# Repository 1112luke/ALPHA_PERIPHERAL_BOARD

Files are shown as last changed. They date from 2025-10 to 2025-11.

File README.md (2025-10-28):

<h1 align="center">🥵🚀NDXP Alpha Peripheral Board🚀🌡️</h1>

<p align="center">
  Screenshot 2025-10-28 at 10 34 32 AM

</p>

<h4 align="center">This is the repository for the HARDWARE DESIGN ONLY. Software for the board can be found <a href="https://github.com/1112luke/NDXPCOMPUTER">here</a></h4>

## Introduction

This board was developed for NDXP's Alpha engine. Its purpose is to serve as a peripheral board to the [F.E.R.B.](https://github.com/1112luke/NDXPCOMPUTER) flight computer, and will facilitate data collection for the secifics of the Alpha mission. The board is responsible for collecting pressure and temperature data on the engine, as well as accelerometer data and load cell data during ground testing.

## Specifications

The board has capability in data collection, communication, actuation, and failsafe:

### Data Collection
- 12x 0-5v ADC (used for pressure sensing)
- 4x Thermocouple Channels
- 1x I2C accelerometer interface
- 1x Load Cell Interface

### Communication
- 1x RS-485 Channel (for communication with  [F.E.R.B.](https://github.com/1112luke/NDXPCOMPUTER))
- 1x Serial USB Port

### Actuation
- 4x Solenoid Valve Channels
- 1x Pyro Channel

### Failsafe
- 2x Keyed Switches (Pyro, Solenoids)
- 1x Burnwire Ignition Detection
- 1x E-STOP

## Contributors
- Luke Scholler
- Sebastian Brock

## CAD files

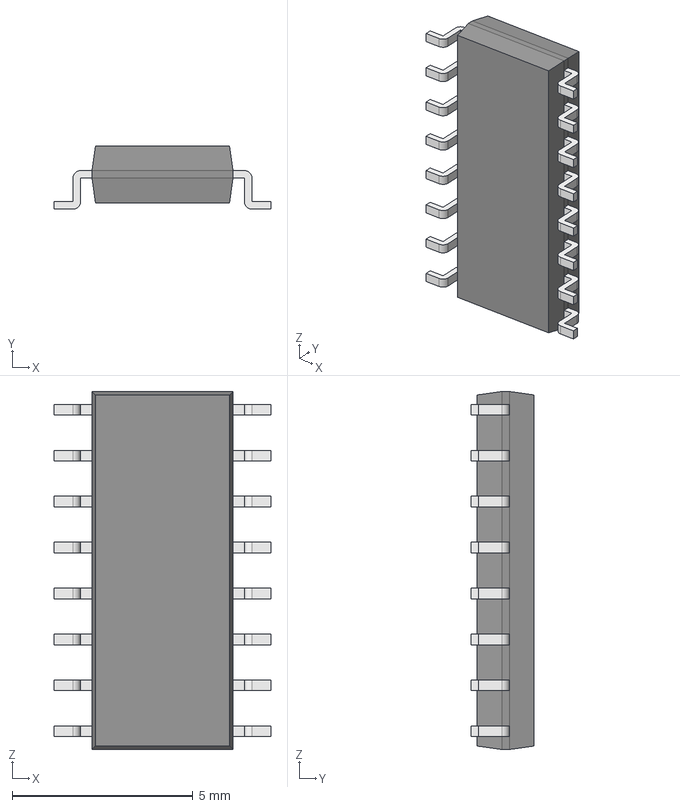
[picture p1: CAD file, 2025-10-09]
Custom_Parts/ADS1231ID/ADS1231ID.step
6.00 x 1.75 x 9.90 mm
Body001 (Mirror #1) x 8
XY-plane x 12
X-axis x 12

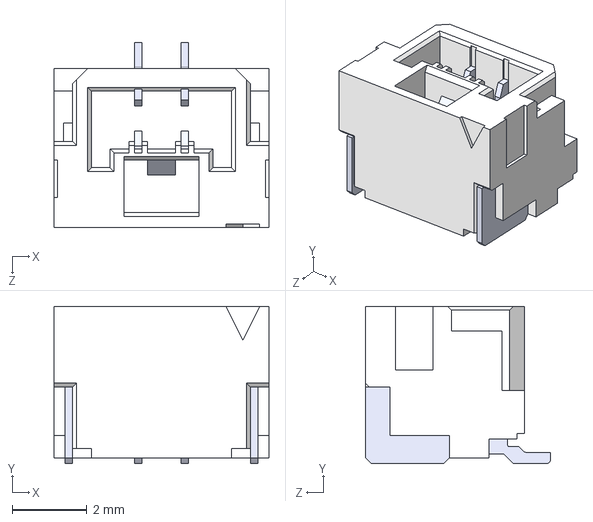
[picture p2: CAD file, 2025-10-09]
Custom_Parts/BM02B-GHS/BM02B-GHS-TBT_LF__SN_.step
5.75 x 4.20 x 4.95 mm

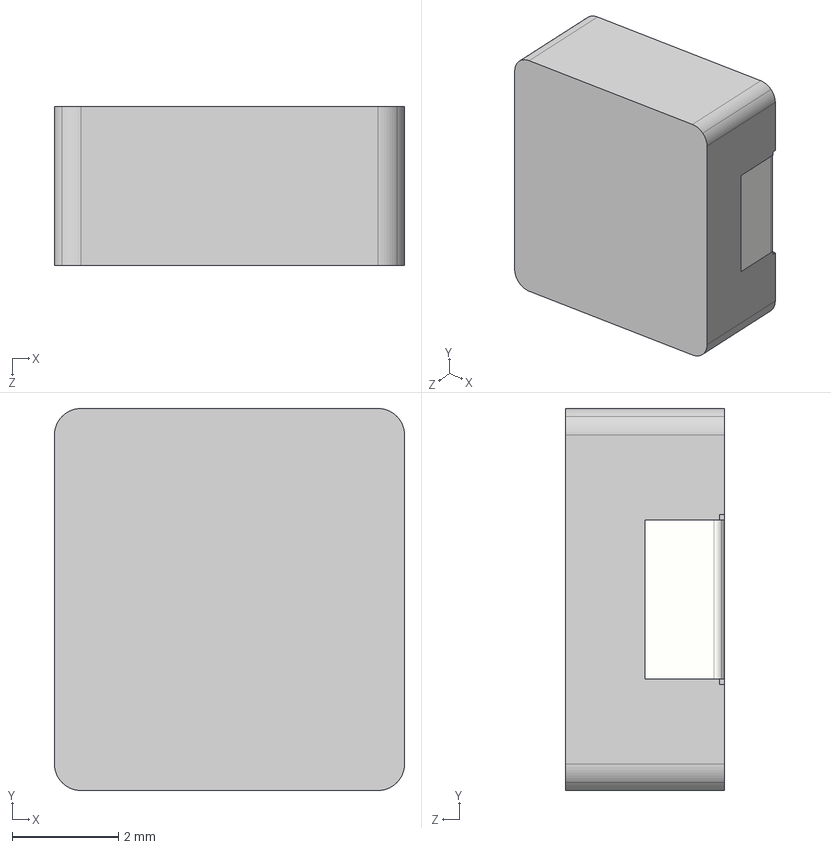
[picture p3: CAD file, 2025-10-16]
Custom_Parts/CYA0630-1.5UH/User Library-L_ShouHan_CYA0630.STEP
6.60 x 7.20 x 3.00 mm

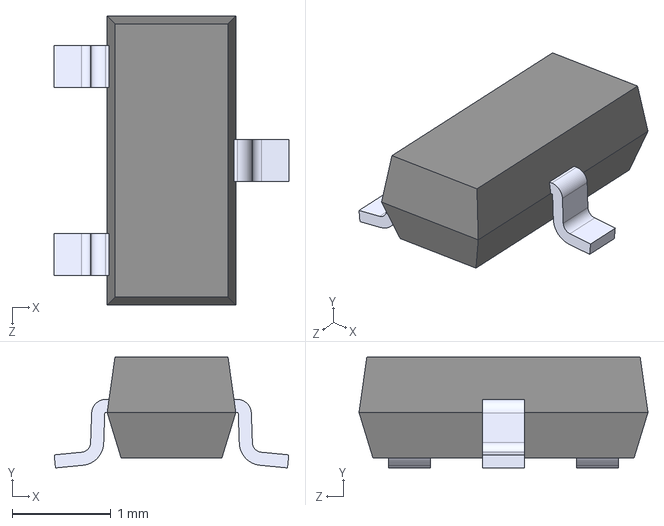
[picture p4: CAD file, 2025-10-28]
Custom_Parts/SI2302/SI2302.step
2.37 x 1.12 x 2.92 mm

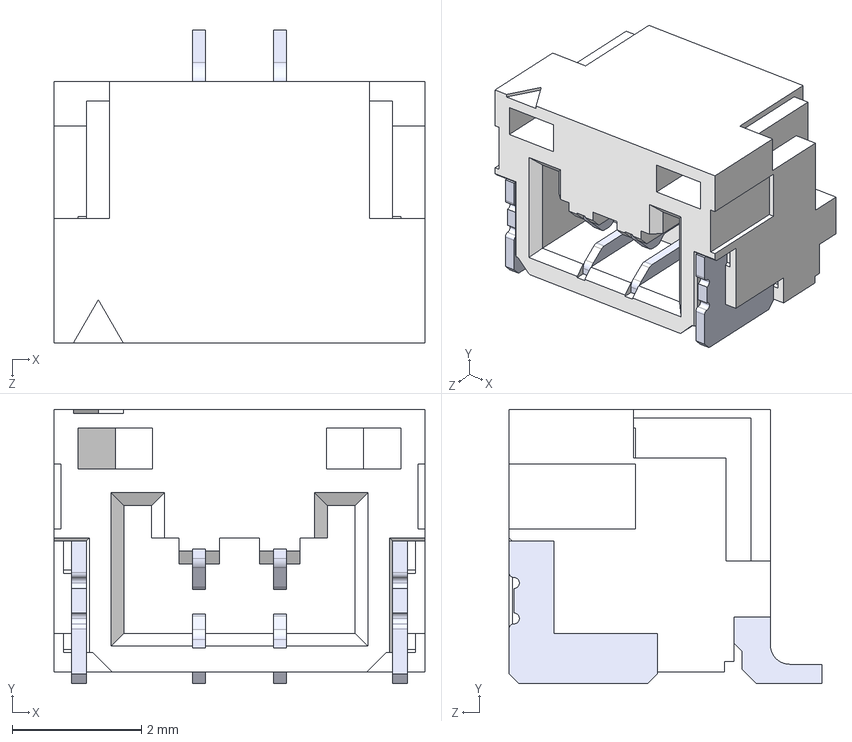
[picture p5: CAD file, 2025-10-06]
Custom_Parts/SM02B-GHS/SM02B-GHS.step
5.75 x 4.25 x 4.85 mm
SMxB-GHS-TB_02
pin x 2

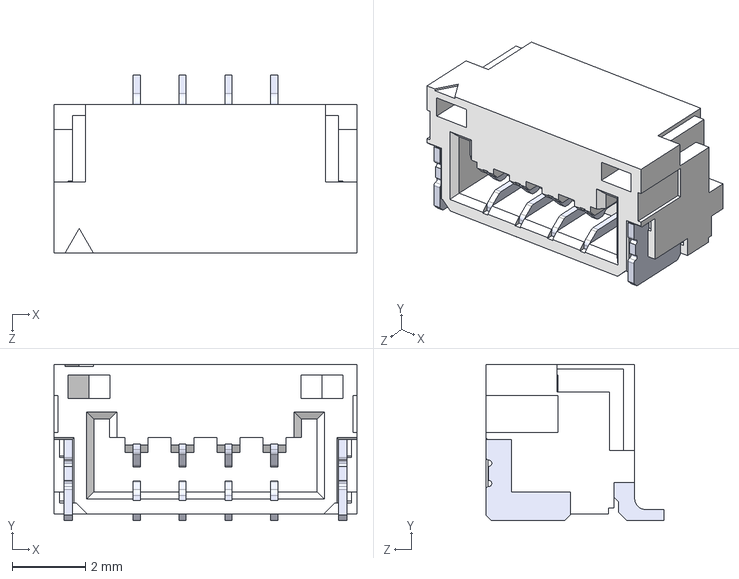
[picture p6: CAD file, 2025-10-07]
Custom_Parts/SM04B-GHS/SM04B-GHS-TB_LF__SN_-.step
8.25 x 4.25 x 4.85 mm
SMxB-GHS-TB_04
pin x 4

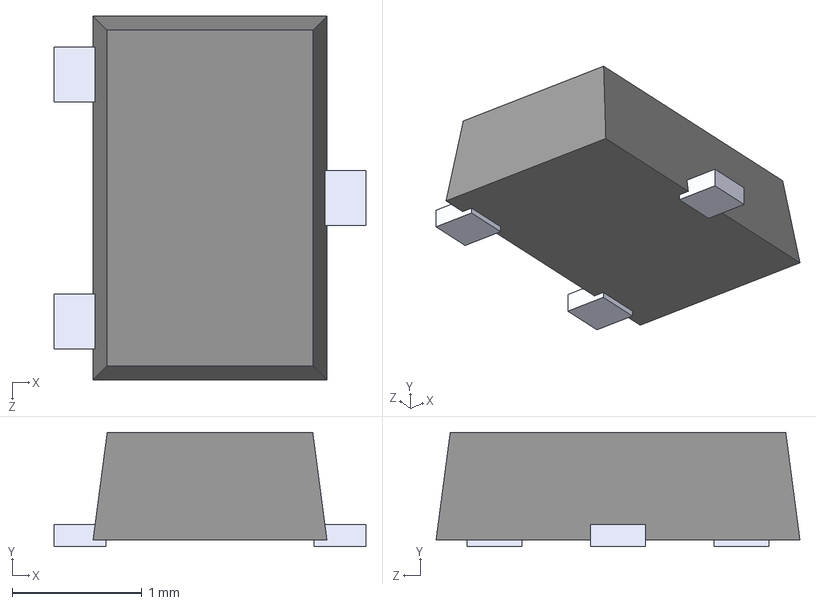
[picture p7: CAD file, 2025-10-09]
Custom_Parts/SSM3J328R/SSM3J328R_LF.step
2.40 x 0.88 x 2.80 mm

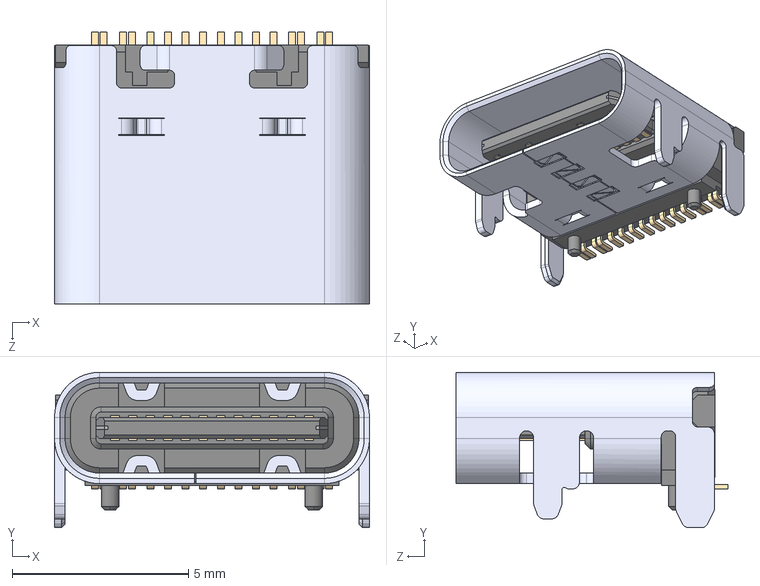
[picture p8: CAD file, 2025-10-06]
Custom_Parts/USB-C/step file.step
8.94 x 4.41 x 7.71 mm

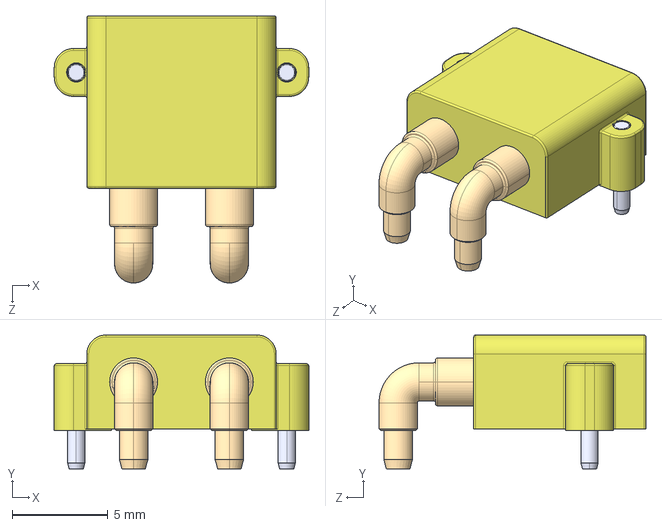
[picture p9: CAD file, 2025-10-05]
Custom_Parts/XT-30/step file.step
13.3 x 7.00 x 14.0 mm

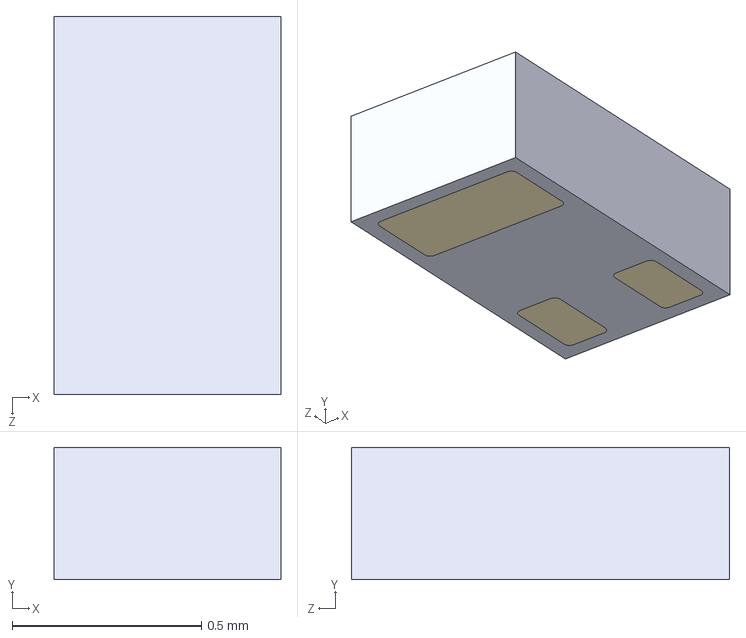
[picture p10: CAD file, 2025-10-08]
Custom_Parts/CSD13381F4/CSD13381F4.step
0.6 x 0.35 x 1.00 mm

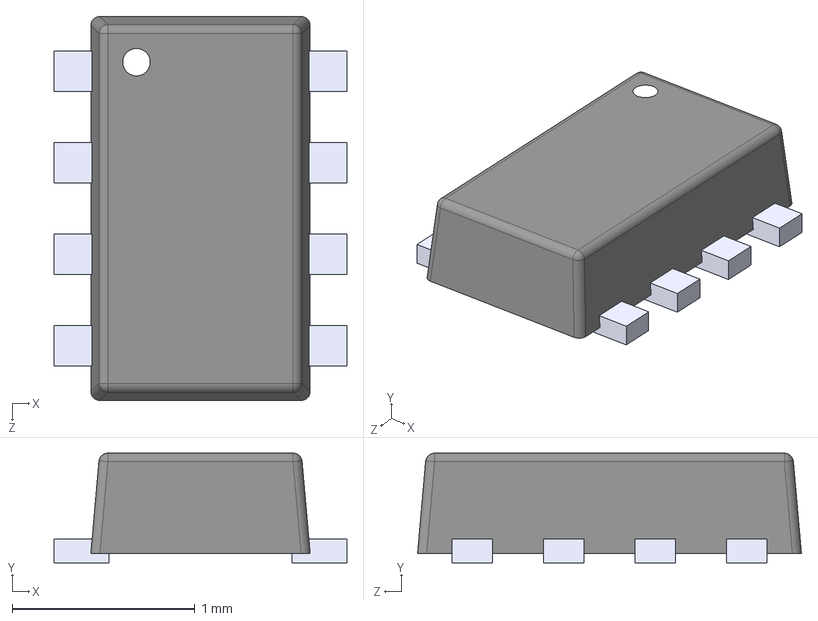
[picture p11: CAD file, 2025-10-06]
Custom_Parts/LM66200DRLR/LM66200DRLR.step
1.60 x 0.6 x 2.10 mm

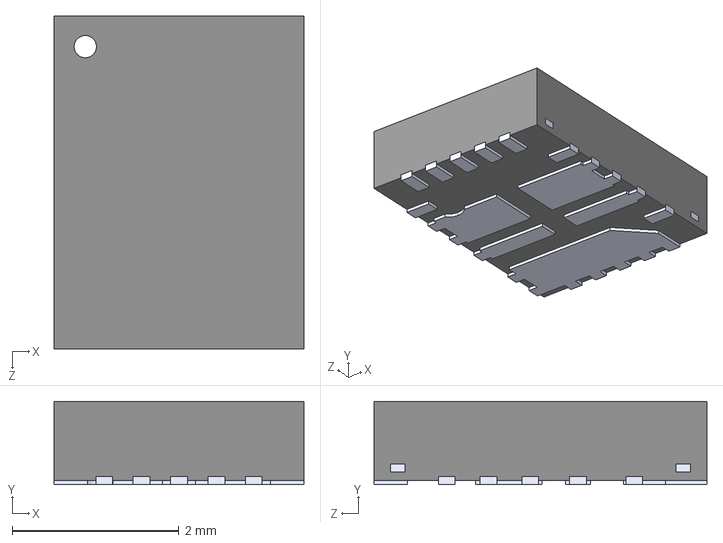
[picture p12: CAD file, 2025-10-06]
Custom_Parts/TPS513885VABR/TPS513885VABR.step
3.00 x 1.00 x 4.00 mm

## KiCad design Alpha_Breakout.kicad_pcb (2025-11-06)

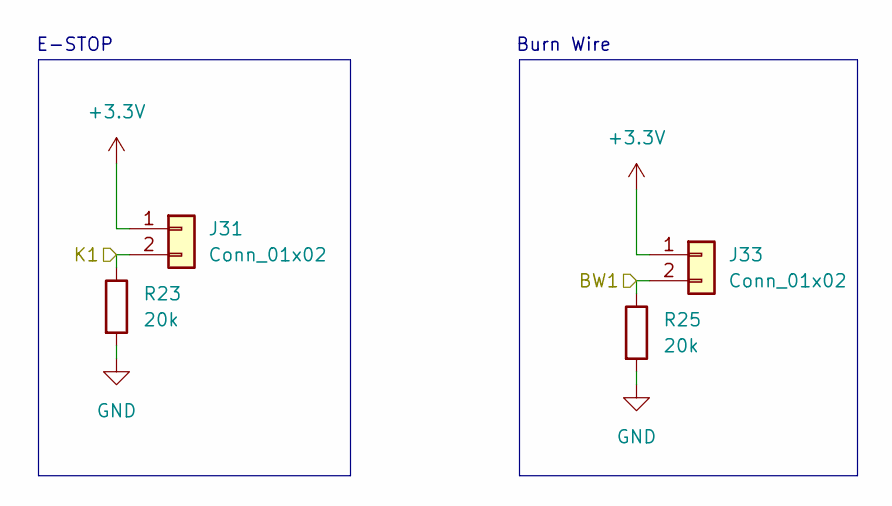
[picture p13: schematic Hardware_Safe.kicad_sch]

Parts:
J31, J33: Conn_01x02; JST_BM02B-GHS-TBT_LF__SN_; JLC# C161690
R23, R25: 20k; R_0402_1005Metric

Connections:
+3.3V: J31.1, J33.1; also elsewhere on the board
/Hardware_Safe/BW1: J33.2, R25.1; also elsewhere on the board
/Hardware_Safe/K1: J31.2, R23.1; also elsewhere on the board
GND: R23.2, R25.2; also elsewhere on the board

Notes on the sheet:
E-STOP
Burn Wire

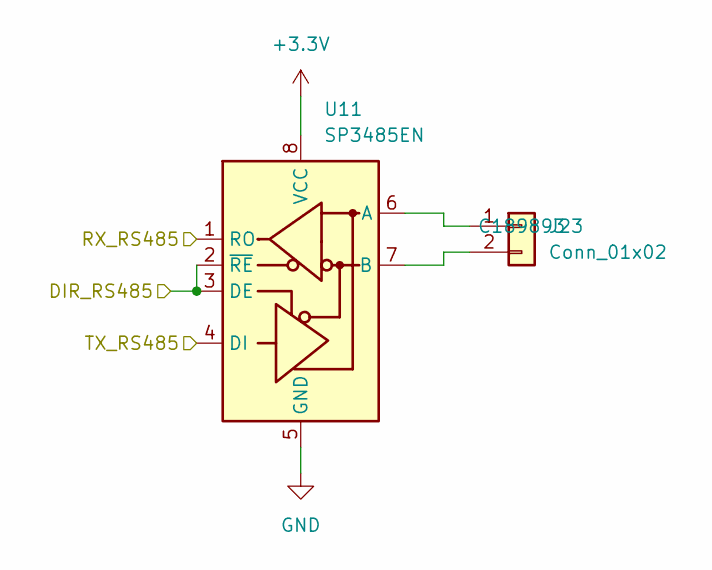
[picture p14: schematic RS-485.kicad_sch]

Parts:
J23: Conn_01x02; CONN_SM02B-GHS_JST; JLC# C189893
U11: SP3485EN; SOIC-8_3.9x4.9mm_P1.27mm; JLC# C8963

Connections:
+3.3V: U11.8 (VCC); also elsewhere on the board
/RS-485/DIR_RS485: U11.2 (~RE), U11.3 (DE); also elsewhere on the board
/RS-485/RX_RS485: U11.1 (RO); also elsewhere on the board
/RS-485/TX_RS485: U11.4 (DI); also elsewhere on the board
GND: U11.5 (GND); also elsewhere on the board
unnamed: J23.1, U11.6 (A)
unnamed: J23.2, U11.7 (B)

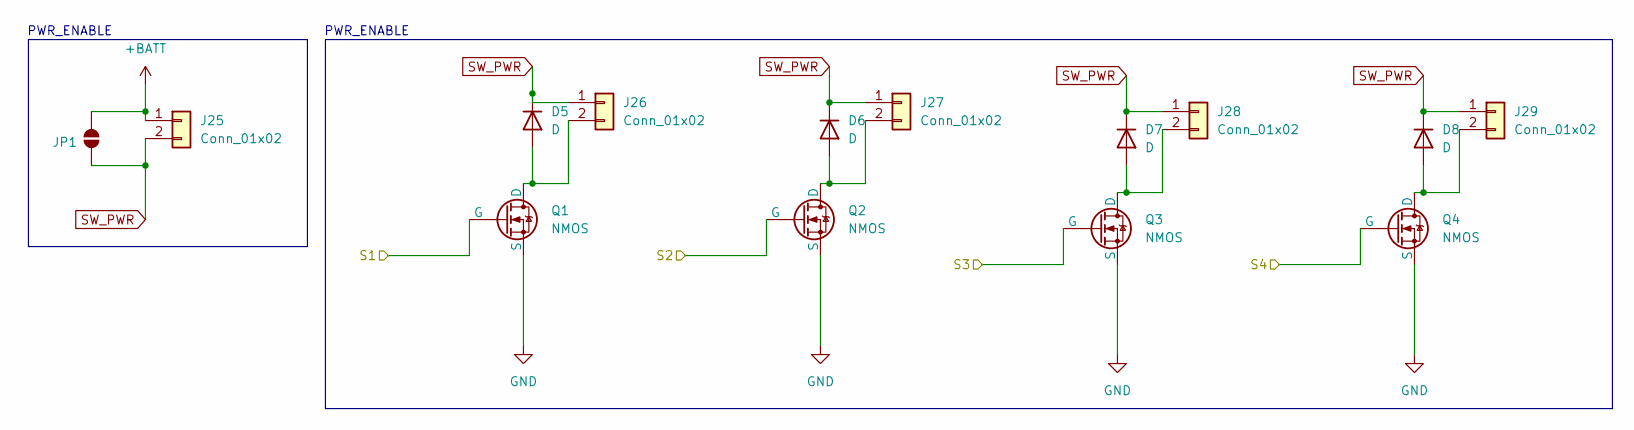
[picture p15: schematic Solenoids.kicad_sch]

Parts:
D5, D6, D7, D8: D; D_SMA; JLC# C8678
J25: Conn_01x02; JST_BM02B-GHS-TBT_LF__SN_; JLC# C161690
J26, J27, J28, J29: Conn_01x02; TerminalBlock_Phoenix_MPT-0,5-2-2.54_1x02_P2.54mm_Horizontal; JLC# C918120
JP1: SolderJumper_2_Open; SolderJumper-2_P1.3mm_Open_TrianglePad1.0x1.5mm
Q1, Q2, Q3, Q4: NMOS; SOT23; JLC# C2891732

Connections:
+BATT: J25.1, JP1.1 (A); also elsewhere on the board
/Solenoids/S1: Q1.2 (G); also elsewhere on the board
/Solenoids/S2: Q2.2 (G); also elsewhere on the board
/Solenoids/S3: Q3.2 (G); also elsewhere on the board
/Solenoids/S4: Q4.2 (G); also elsewhere on the board
GND: Q1.3 (S), Q2.3 (S), Q3.3 (S), Q4.3 (S); also elsewhere on the board
unnamed: D5.2 (A), J26.2, Q1.1 (D)
unnamed: D6.2 (A), J27.2, Q2.1 (D)
unnamed: D7.2 (A), J28.2, Q3.1 (D)
unnamed: D8.2 (A), J29.2, Q4.1 (D)
SW_PWR: D5.1 (K), D6.1 (K), D7.1 (K), D8.1 (K), J25.2, J26.1, J27.1, J28.1, J29.1, JP1.2 (B)

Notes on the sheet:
PWR_ENABLE

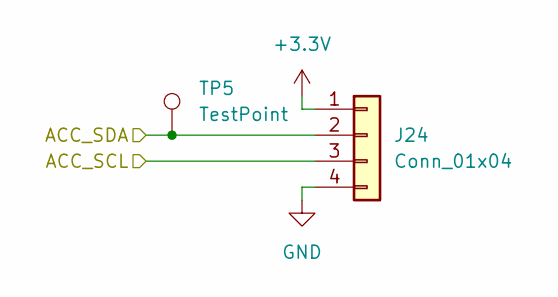
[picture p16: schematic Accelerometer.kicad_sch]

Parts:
J24: Conn_01x04; JST_GH_SM04B-GHS-TB_1x04-1MP_P1.25mm_Horizontal; JLC# C189895
TP5: TestPoint; TestPoint_Pad_D1.0mm

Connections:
+3.3V: J24.1; also elsewhere on the board
/Accelerometer/ACC_SCL: J24.3; also elsewhere on the board
/Accelerometer/ACC_SDA: J24.2, TP5.1; also elsewhere on the board
GND: J24.4; also elsewhere on the board

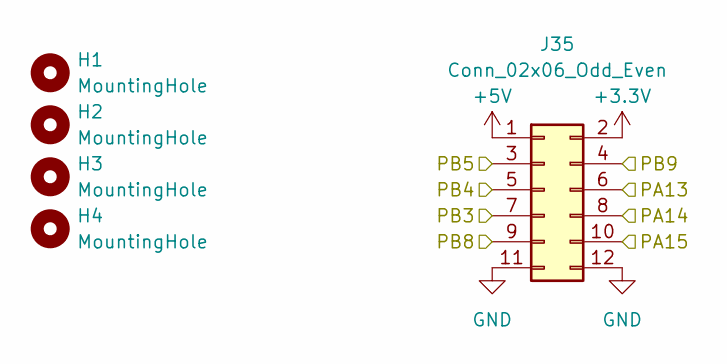
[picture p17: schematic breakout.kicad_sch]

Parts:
H1, H2, H3, H4: MountingHole; MountingHole_2.2mm_M2_DIN965_Pad
J35: Conn_02x06_Odd_Even; PinHeader_2x06_P2.54mm_Vertical

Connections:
+3.3V: J35.2; also elsewhere on the board
+5V: J35.1; also elsewhere on the board
/Breakout/PA13: J35.6; also elsewhere on the board
/Breakout/PA14: J35.8; also elsewhere on the board
/Breakout/PA15: J35.10; also elsewhere on the board
/Breakout/PB3: J35.7; also elsewhere on the board
/Breakout/PB4: J35.5; also elsewhere on the board
/Breakout/PB5: J35.3; also elsewhere on the board
/Breakout/PB8: J35.9; also elsewhere on the board
/Breakout/PB9: J35.4; also elsewhere on the board
GND: J35.11, J35.12; also elsewhere on the board

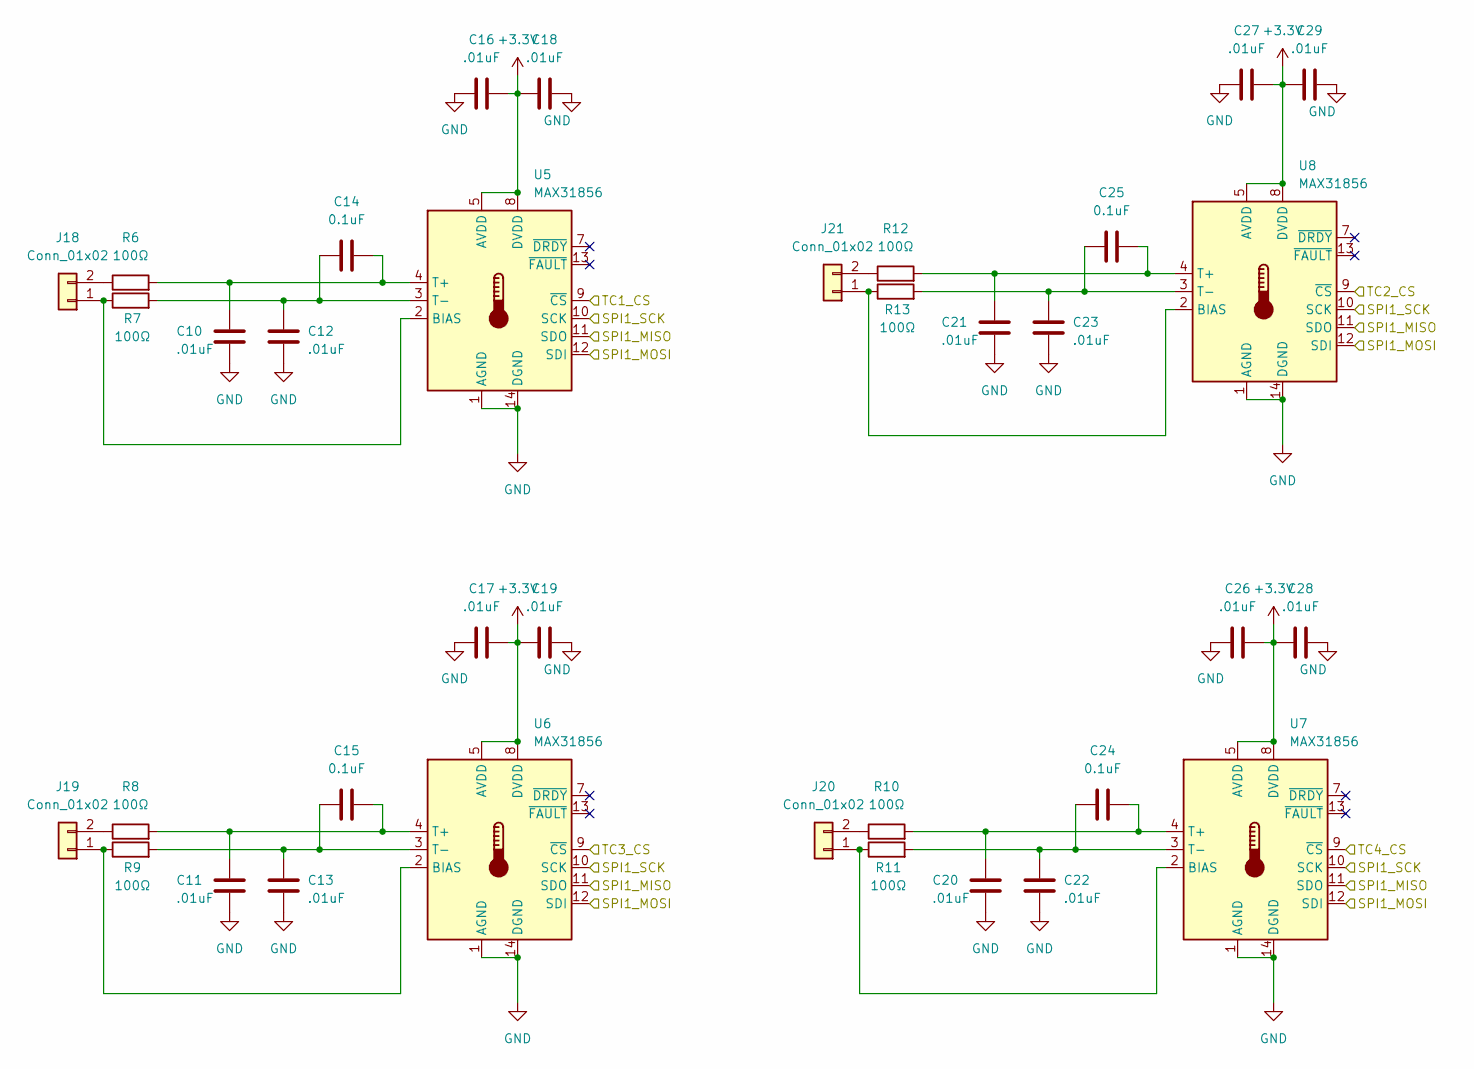
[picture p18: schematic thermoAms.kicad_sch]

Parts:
C10, C11, C12, C13, C16, C17, C18, C19, C20, C21, C22, C23, C26, C27, C28, C29: .01uF; C_0402_1005Metric
C14, C15, C24, C25: 0.1uF; C_0402_1005Metric
J18, J19, J20, J21: Conn_01x02; TerminalBlock_Phoenix_MPT-0,5-2-2.54_1x02_P2.54mm_Horizontal; JLC# C918120
R6, R7, R8, R9, R10, R11, R12, R13: 100Ω; R_0402_1005Metric
U5, U6, U7, U8: MAX31856; TSSOP-14_4.4x5mm_P0.65mm; JLC# C2653162

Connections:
+3.3V: C16.2, C17.2, C18.1, C19.1, C26.2, C27.2, C28.1, C29.1, U5.5 (AVDD), U5.8 (DVDD), U6.5 (AVDD), U6.8 (DVDD), U7.5 (AVDD), U7.8 (DVDD), U8.5 (AVDD), U8.8 (DVDD); also elsewhere on the board
/stm32f1/SPI1_MISO: U5.11 (SDO), U6.11 (SDO), U7.11 (SDO), U8.11 (SDO); also elsewhere on the board
/stm32f1/SPI1_MOSI: U5.12 (SDI), U6.12 (SDI), U7.12 (SDI), U8.12 (SDI); also elsewhere on the board
/stm32f1/SPI1_SCK: U5.10 (SCK), U6.10 (SCK), U7.10 (SCK), U8.10 (SCK); also elsewhere on the board
/stm32f1/TC1_CS: U5.9 (~CS); also elsewhere on the board
/stm32f1/TC2_CS: U8.9 (~CS); also elsewhere on the board
/stm32f1/TC3_CS: U6.9 (~CS); also elsewhere on the board
/stm32f1/TC4_CS: U7.9 (~CS); also elsewhere on the board
GND: C10.1, C11.1, C12.1, C13.1, C16.1, C17.1, C18.2, C19.2, C20.1, C21.1, C22.1, C23.1, C26.1, C27.1, C28.2, C29.2, U5.1 (AGND), U5.14 (DGND), U6.1 (AGND), U6.14 (DGND), U7.1 (AGND), U7.14 (DGND), U8.1 (AGND), U8.14 (DGND); also elsewhere on the board
unnamed: J18.1, R7.1, U5.2 (BIAS)
unnamed: J18.2, R6.1
unnamed: J19.1, R9.1, U6.2 (BIAS)
unnamed: J19.2, R8.1
unnamed: J20.1, R11.1, U7.2 (BIAS)
unnamed: J20.2, R10.1
unnamed: J21.1, R13.1, U8.2 (BIAS)
unnamed: J21.2, R12.1
unnamed: C10.2, C14.1, R6.2, U5.4 (T+)
unnamed: C12.2, C14.2, R7.2, U5.3 (T-)
unnamed: C11.2, C15.1, R8.2, U6.4 (T+)
unnamed: C13.2, C15.2, R9.2, U6.3 (T-)
unnamed: C20.2, C24.1, R10.2, U7.4 (T+)
unnamed: C22.2, C24.2, R11.2, U7.3 (T-)
unnamed: C21.2, C25.1, R12.2, U8.4 (T+)
unnamed: C23.2, C25.2, R13.2, U8.3 (T-)

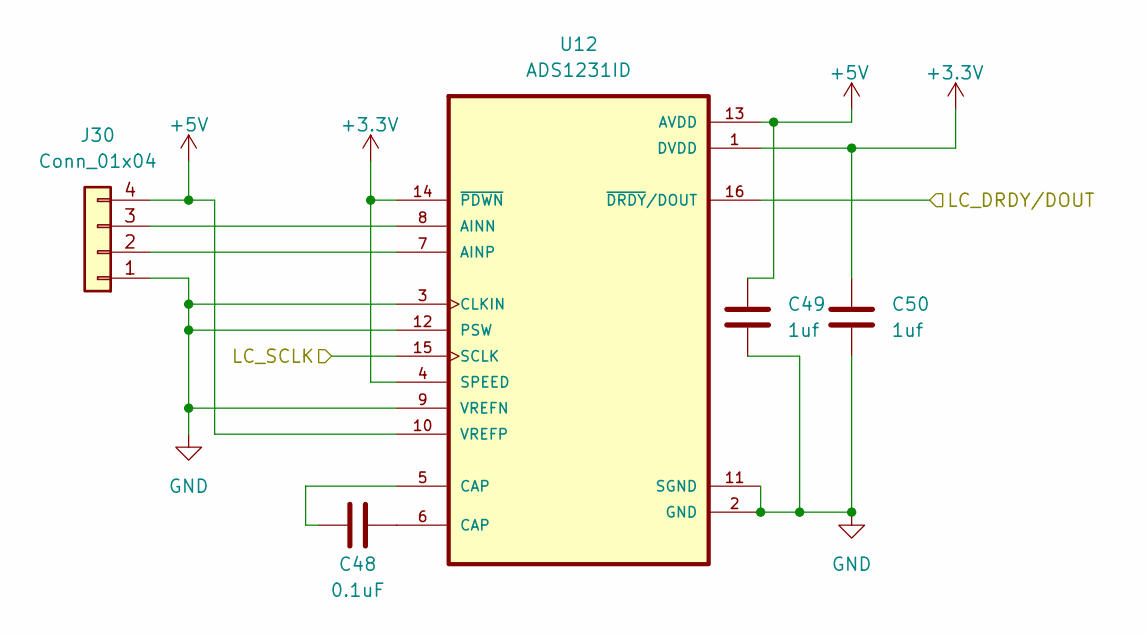
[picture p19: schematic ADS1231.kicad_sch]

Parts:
C48: 0.1uF; C_0402_1005Metric
C49, C50: 1uf; C_0402_1005Metric
J30: Conn_01x04; JST_SM04B-GHS-TB_LF__SN_-; JLC# C189895
U12: ADS1231ID; SOIC127P600X175-16N; JLC# C486034

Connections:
+3.3V: C50.2, U12.1 (DVDD), U12.4 (SPEED), U12.14 (~PDWN); also elsewhere on the board
+5V: C49.1, J30.4, U12.10 (VREFP), U12.13 (AVDD); also elsewhere on the board
/ADS1231/LC_DRDY/DOUT: U12.16 (~DRDY/DOUT); also elsewhere on the board
/ADS1231/LC_SCLK: U12.15 (SCLK); also elsewhere on the board
GND: C49.2, C50.1, J30.1, U12.2 (GND), U12.3 (CLKIN), U12.9 (VREFN), U12.11 (SGND), U12.12 (PSW); also elsewhere on the board
unnamed: C48.1, U12.6 (CAP)
unnamed: C48.2, U12.5 (CAP)
unnamed: J30.2, U12.7 (AINP)
unnamed: J30.3, U12.8 (AINN)

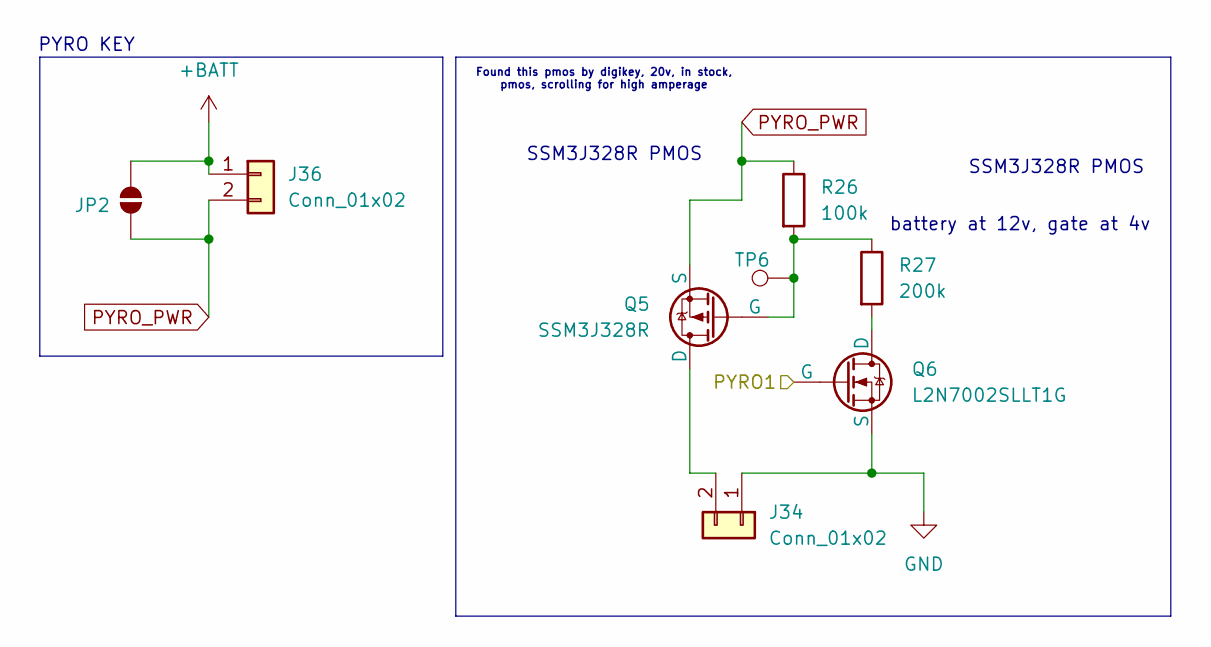
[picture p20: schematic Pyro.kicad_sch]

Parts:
J34: Conn_01x02; PinHeader_1x02_P2.54mm_Vertical
J36: Conn_01x02; JST_XH_B2B-XH-A_1x02_P2.50mm_Vertical; JLC# C158012
JP2: SolderJumper_2_Open; SolderJumper-2_P1.3mm_Open_TrianglePad1.0x1.5mm
Q5: SSM3J328R; SOT95P240X88-3N; JLC# C396016
Q6: L2N7002SLLT1G; SOT-23; JLC# C22446827
R26: 100k; R_0603_1608Metric
R27: 200k; R_0603_1608Metric
TP6: TestPoint; TestPoint_Pad_D1.0mm

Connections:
+BATT: J36.1, JP2.1 (A); also elsewhere on the board
/Pyro/PYRO1: Q6.2 (G); also elsewhere on the board
GND: J34.1, Q6.3 (S); also elsewhere on the board
unnamed: J34.2, Q5.1 (D)
unnamed: Q5.2 (G), R26.2, R27.1, TP6.1
unnamed: Q6.1 (D), R27.2
PYRO_PWR: J36.2, JP2.2 (B), Q5.3 (S), R26.1

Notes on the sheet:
PYRO KEY
SSM3J328R PMOS
battery at 12v, gate at 4v
Found this pmos by digikey, 20v, in stock, pmos, scrolling for high amperage

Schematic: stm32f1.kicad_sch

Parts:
C1, C2, C3, C4, C6: 100nF; C_0402_1005Metric
C5: 10uF; C_0805_2012Metric
C7: 1uF; C_0603_1608Metric
D9: Red; LED_0603_1608Metric; JLC# C19171390
D10: White; LED_0603_1608Metric; JLC# C19273150
D11: Blue; LED_0603_1608Metric; JLC# C19171394
R1, R2: 4.7K; R_0402_1005Metric
R3: 10k; R_0603_1608Metric
R28, R29, R30: 100Ω; R_0402_1005Metric
SW1, SW2: SW_Push; SW_SPST_B3U-1000P; JLC# C231329
U1: STM32F103C8Tx; LQFP-48_7x7mm_P0.5mm; JLC# C8734

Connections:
+3.3V: C2.1, C3.1, C4.1, C5.1, C6.1, C7.1, R1.1, R2.1, R28.1, R29.1, R30.1, SW2.1, U1.1 (VBAT), U1.9 (VDDA), U1.24 (VDD), U1.36 (VDD), U1.48 (VDD); also elsewhere on the board
/ADCs/SCL: R1.2, U1.42 (PB6); also elsewhere on the board
/ADCs/SDA: R2.2, U1.43 (PB7); also elsewhere on the board
/ADS1231/LC_DRDY/DOUT: U1.32 (PA11); also elsewhere on the board
/ADS1231/LC_SCLK: U1.33 (PA12); also elsewhere on the board
/Accelerometer/ACC_SCL: U1.22 (PB11); also elsewhere on the board
/Accelerometer/ACC_SDA: U1.21 (PB10); also elsewhere on the board
/Breakout/PA13: U1.34 (PA13); also elsewhere on the board
/Breakout/PA14: U1.37 (PA14); also elsewhere on the board
/Breakout/PA15: U1.38 (PA15); also elsewhere on the board
/Breakout/PB3: U1.39 (PB3); also elsewhere on the board
/Breakout/PB4: U1.40 (PB4); also elsewhere on the board
/Breakout/PB5: U1.41 (PB5); also elsewhere on the board
/Breakout/PB8: U1.45 (PB8); also elsewhere on the board
/Breakout/PB9: U1.46 (PB9); also elsewhere on the board
/Hardware_Safe/BW1: U1.20 (PB2); also elsewhere on the board
/Hardware_Safe/K1: U1.5 (PD0); also elsewhere on the board
/Pyro/PYRO1: U1.29 (PA8); also elsewhere on the board
/RS-485/DIR_RS485: U1.14 (PA4); also elsewhere on the board
/RS-485/RX_RS485: U1.13 (PA3); also elsewhere on the board
/RS-485/TX_RS485: U1.12 (PA2); also elsewhere on the board
/Solenoids/S1: U1.25 (PB12); also elsewhere on the board
/Solenoids/S2: U1.26 (PB13); also elsewhere on the board
/Solenoids/S3: U1.27 (PB14); also elsewhere on the board
/Solenoids/S4: U1.28 (PB15); also elsewhere on the board
/prog/USB_RX: U1.30 (PA9); also elsewhere on the board
/prog/USB_TX: U1.31 (PA10); also elsewhere on the board
/stm32f1/SPI1_MISO: U1.16 (PA6); also elsewhere on the board
/stm32f1/SPI1_MOSI: U1.17 (PA7); also elsewhere on the board
/stm32f1/SPI1_SCK: U1.15 (PA5); also elsewhere on the board
/stm32f1/TC1_CS: U1.18 (PB0); also elsewhere on the board
/stm32f1/TC2_CS: U1.19 (PB1); also elsewhere on the board
/stm32f1/TC3_CS: U1.11 (PA1); also elsewhere on the board
/stm32f1/TC4_CS: U1.10 (PA0); also elsewhere on the board
GND: C1.2, C2.2, C3.2, C4.2, C5.2, C6.2, C7.2, R3.2, SW1.1, U1.8 (VSSA), U1.23 (VSS), U1.35 (VSS), U1.47 (VSS); also elsewhere on the board
unnamed: D9.2 (A), R28.2
unnamed: D9.1 (K), U1.2 (PC13)
unnamed: D10.2 (A), R29.2
unnamed: D10.1 (K), U1.3 (PC14)
unnamed: D11.2 (A), R30.2
unnamed: D11.1 (K), U1.4 (PC15)
unnamed: R3.1, SW2.2, U1.44 (BOOT0)
unnamed: C1.1, SW1.2, U1.7 (NRST)

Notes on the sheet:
I2C Pullup
for VDD Pins
for vdda

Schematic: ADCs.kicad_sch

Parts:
C8, C9: 1uF; C_0603_1608Metric
J3, J4, J5, J7, J8, J9, J10, J11, J12, J14, J15, J16: Conn_01x03; TerminalBlock_Phoenix_MPT-0,5-3-2.54_1x03_P2.54mm_Horizontal; JLC# C918121
R22, R33: 4.7K; R_0402_1005Metric
R31, R32: 5Ω; R_0402_1005Metric
U3, U4: ADS7828; TSSOP-16_4.4x5mm_P0.65mm; JLC# C701649
U13: TCA9517ADGK; VSSOP-8_3x3mm_P0.65mm; JLC# C201698

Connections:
+3.3V: U13.1 (VCCA); also elsewhere on the board
+5V: J3.1, J4.1, J5.1, J7.1, J8.1, J9.1, J10.1, J11.1, J12.1, J14.1, J15.1, J16.1, R22.1, R31.1, R32.1, R33.1, U3.10 (REF), U4.10 (REF), U4.12 (A0), U13.8 (VCCB); also elsewhere on the board
/ADCs/SCL: U13.2 (SCLA); also elsewhere on the board
/ADCs/SDA: U13.3 (SDAA); also elsewhere on the board
CH_02: J10.2, U3.3 (CH2)
CH_03: J14.2, U3.4 (CH3)
CH_04: J3.2, U3.5 (CH4)
CH_05: J7.2, U3.6 (CH5)
CH_06: J11.2, U3.7 (CH6)
CH_07: J15.2, U3.8 (CH7)
CH_08: J4.2, U4.1 (CH0)
CH_09: J8.2, U4.2 (CH1)
CH_10: J12.2, U4.3 (CH2)
CH_11: J16.2, U4.4 (CH3)
CH_12: J5.2, U4.5 (CH4)
CH_13: J9.2, U4.6 (CH5)
GND: C8.2, C9.2, J3.3, J4.3, J5.3, J7.3, J8.3, J9.3, J10.3, J11.3, J12.3, J14.3, J15.3, J16.3, U3.9 (GND), U3.11 (COM), U3.12 (A0), U3.13 (A1), U4.9 (GND), U4.11 (COM), U4.13 (A1), U13.4 (GND); also elsewhere on the board
unnamed: C8.1, R31.2, U3.16 (VDD)
unnamed: C9.1, R32.2, U4.16 (VDD)
SCL_5V: R22.2, U3.14 (SCL), U4.14 (SCL), U13.7 (SCLB)
SDA_5V: R33.2, U3.15 (SDA), U4.15 (SDA), U13.6 (SDAB)

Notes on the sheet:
Terminal Blocks
Analog -> Digital
Level Shifter
internal pullup to VCCB

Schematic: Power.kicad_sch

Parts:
C30: 470pF; C_0402_1005Metric
C31, C38: 100nF; C_0402_1005Metric
C32: 10uF; C_0805_2012Metric
C33: 2.2uF; C_0603_1608Metric
C34, C37, C40: 22uF; C_1206_3216Metric; JLC# C12891
C35, C36, C39, C41, C42, C44: 22uF; C_1206_3216Metric
C43: 100nF; C_0402_1005Metric; JLC# C60474
C45: 1uF; C_0402_1005Metric; JLC# C29266
C46: 2.2uF; C_0402_1005Metric
C47: 10nF; C_0402_1005Metric
D1, D2, D4: White; LED_0603_1608Metric; JLC# C19273150
D3: BLUE; LED_0603_1608Metric; JLC# C19171394
IC1: LM66200DRLR; SOT8; JLC# C3235556
J22: Conn_01x02; AMASS_XT30PW-M_1x02_P2.50mm_Horizontal; JLC# C431092
L1: 1.5uH; IND_CYA0630_SHH; JLC# C5189745
L2: 4.7uH; L_Changjiang_FNR4030S; JLC# C167874
PS1: TPS513885VABR; CONV_TPS513885VABR; PARTREV B; JLC# C41935536
R14: 1k; R_0402_1005Metric
R15, R17: 0Ω; R_0402_1005Metric
R16: 100k; R_0603_1608Metric
R18, R20, R21: 100Ω; R_0402_1005Metric
R19: 200Ω; R_0402_1005Metric
TP4: TestPoint; TestPoint_Pad_D1.0mm
U9: AP63203WU; TSOT-23-6; JLC# C780769
U10: LP2985-3.3; SOT-23-5; JLC# C95414

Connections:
+3.3V: C36.1, C41.1, L2.2, R18.1, U9.1 (FB); also elsewhere on the board
+5V: C32.1, IC1.2 (VOUT@1), IC1.7 (VOUT@2), R20.1, TP4.1, U9.2 (EN), U9.3 (IN); also elsewhere on the board
+BATT: C34.1, C37.1, C40.1, C43.1, C45.1, J22.2, PS1.1 (VIN), U10.1 (VIN), U10.3 (ON/~OFF); also elsewhere on the board
BATT_V+: C35.1, C39.1, C42.1, C44.1, IC1.3 (VIN1), L1.2, R17.1, R19.1
FB: C30.1, PS1.8 (VOUT), R17.2
GND: C32.2, C33.1, C34.2, C35.2, C36.2, C37.2, C39.2, C40.2, C41.2, C42.2, C43.2, C44.2, C45.2, C46.2, C47.2, D1.1 (K), D2.1 (K), D4.1 (K), IC1.1 (GND@1), IC1.4 (ON), IC1.5 (GND@2), J22.1, PS1.3 (PGND), PS1.11 (PGND), U9.4 (GND), U10.2 (GND); also elsewhere on the board
unnamed: C30.2, R14.1
unnamed: C31.1, R15.1
unnamed: C31.2, L1.1, PS1.2 (SW), PS1.12 (SW)
unnamed: D1.2 (A), R18.2
unnamed: D2.2 (A), R19.2
unnamed: D3.2 (A), R20.2
unnamed: D3.1 (K), IC1.8 (ST), R21.1
unnamed: D4.2 (A), R21.2
unnamed: PS1.7 (FB), R14.2
unnamed: PS1.4 (PG), R16.1
unnamed: PS1.13 (VBST), R15.2
unnamed: C33.2, PS1.10 (VCC), R16.2
unnamed: C38.2, U9.6 (BST)
unnamed: C38.1, L2.1, U9.5 (SW)
unnamed: C47.1, U10.4 (BP)
USB_V+: IC1.6 (VIN2); also elsewhere on the board
en: C46.1, PS1.5 (MODE), PS1.6 (EN), U10.5 (VOUT)

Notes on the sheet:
Battery
TODO: ensure all parts here are rated for voltage/amperage
Dual Diode
3.3v Switching Regulator
5v Switching Regulator
Enable Reg (3.3v)

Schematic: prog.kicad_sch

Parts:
J2: USB_C_Receptacle_USB2.0_16P; USB_C_Receptacle_GCT_USB4105-xx-A_16P_TopMnt_Horizontal; JLC# C2765186
R4, R5: 5.1k; R_0402_1005Metric
TP1: TestPoint; TestPoint_Pad_D1.0mm
U2: CH340N; JEITA_SOIC-8_3.9x4.9mm_P1.27mm; JLC# C2977777

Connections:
+3.3V: U2.5 (VCC), U2.8 (V3); also elsewhere on the board
/prog/USB_RX: U2.7 (RXD); also elsewhere on the board
/prog/USB_TX: TP1.1, U2.6 (TXD); also elsewhere on the board
GND: J2.A1 (GND), J2.A12 (GND), J2.B1 (GND), J2.B12 (GND), J2.S1 (SHIELD), R4.2, R5.2, U2.3 (GND); also elsewhere on the board
unnamed: J2.A5 (CC1), R5.1
unnamed: J2.B5 (CC2), R4.1
unnamed: J2.A6 (D+), J2.B6 (D+), U2.1 (UD+)
unnamed: J2.A7 (D-), J2.B7 (D-), U2.2 (UD-)
USB_V+: J2.A4 (VBUS), J2.A9 (VBUS), J2.B4 (VBUS), J2.B9 (VBUS); also elsewhere on the board

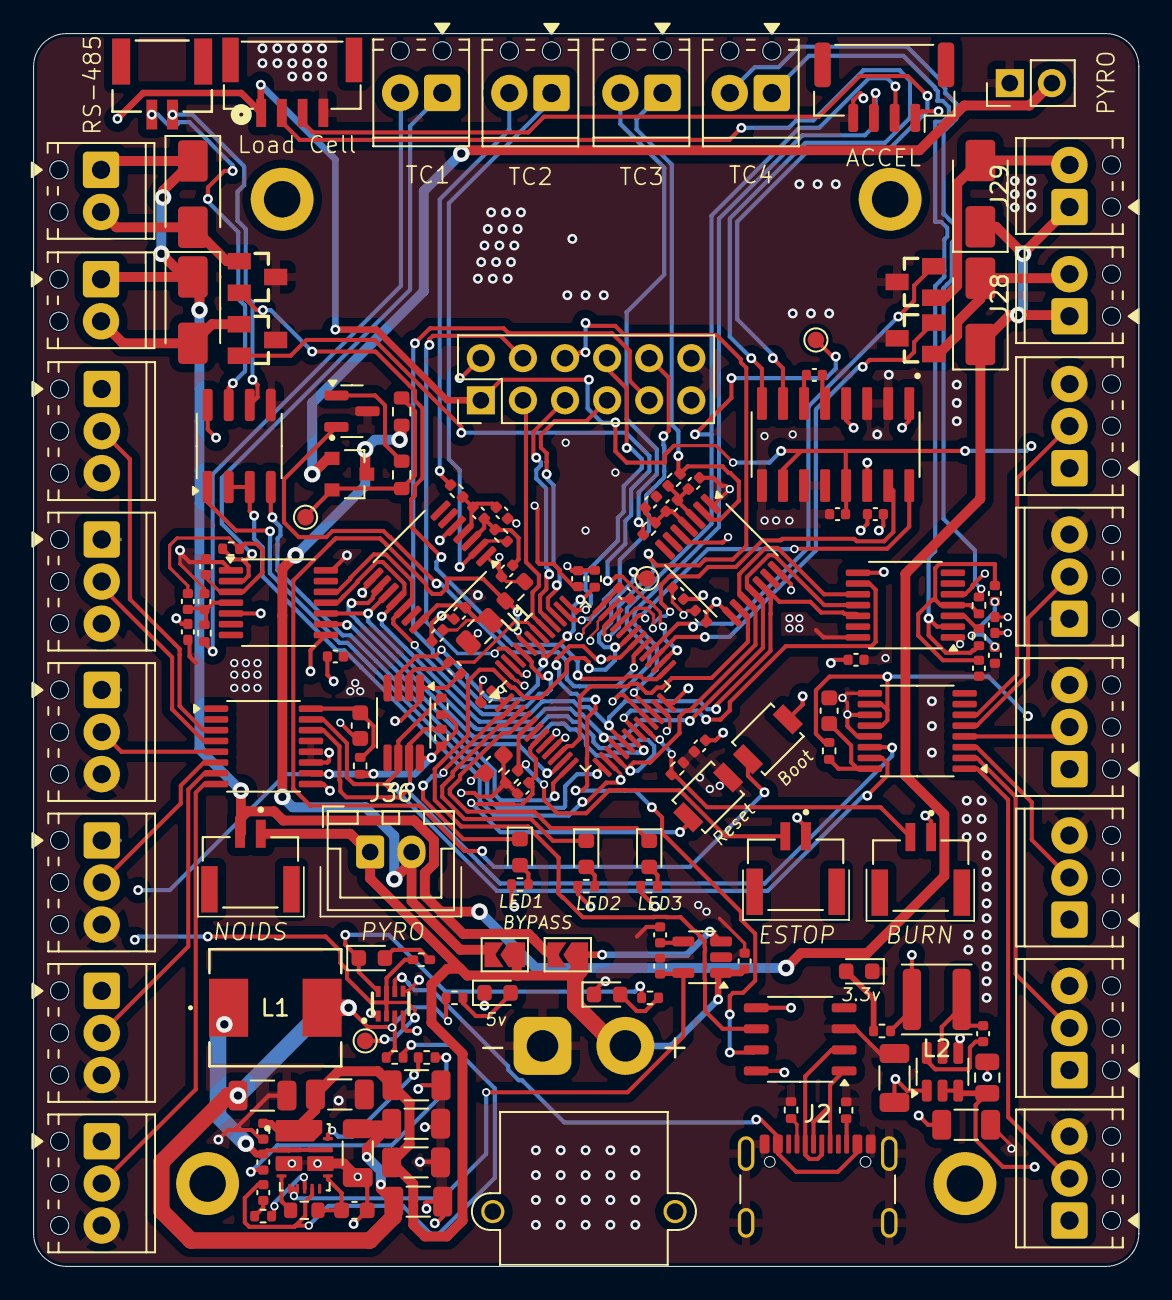
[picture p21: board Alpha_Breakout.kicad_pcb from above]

Board: 4 copper layers, 66.7 x 74.4 mm, 159 parts (0 on the bottom side), 115 nets.

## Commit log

2025-10-05 initial ⚡️
    [Alpha_Breakout.kicad_pcb, Alpha_Breakout.kicad_sch, prog.kicad_sch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]
2025-10-05 added luke name
    [ADCs.kicad_sch, Alpha_Breakout.kicad_pcb, Alpha_Breakout.kicad_sch]
2025-10-05 Textbox Test
    [Alpha_Breakout.kicad_sch]
2025-10-05 Added Thermocouple Amp sheet
    [Alpha_Breakout.kicad_sch, thermoAms.kicad_sch]
2025-10-05 Completed schematic for one IC
    [thermoAms.kicad_sch]
2025-10-06 reg🟡
    [ADCs.kicad_sch, Alpha_Breakout.kicad_pcb, Alpha_Breakout.kicad_sch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]
2025-10-06 layout🏄‍♂️
    [ADCs.kicad_sch, Alpha_Breakout.kicad_pcb, LM66200DRLR.step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]
2025-10-06 Added thermocouple footprints
    8205 used in case we end up hand soldering this thing
    [thermoAms.kicad_sch]
2025-10-06 Routed ThermoAmps to STM32
    [Alpha_Breakout.kicad_sch]
2025-10-06 thermo🌡️
    [Alpha_Breakout.kicad_pcb, thermoAms.kicad_sch]
2025-10-06 Fixed Filters on ADCs
    [ADCs.kicad_sch]
2025-10-06 fixed power
    [Power.kicad_sch]
2025-10-06 added 2 pin connector files for rs232
    [SM02B-GHS.step]
2025-10-07 plug🔌
    [Accelerometer.kicad_sch, Alpha_Breakout.kicad_pcb, Alpha_Breakout.kicad_sch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]
2025-10-08 Added Solenoids (Double Check Diode Type?)
    [Alpha_Breakout.kicad_pcb, Alpha_Breakout.kicad_sch, CSD13381F4.step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]
2025-10-08 oops I forgot to specify resistor footprint
    [Alpha_Breakout.kicad_sch, Power.kicad_sch, Solenoids.kicad_sch]
2025-10-08 Revmoed Diodes (Built in to MOSFET)
    [Solenoids.kicad_sch]
2025-10-08 Put Diodes Back
2025-10-08 Removed extraneous Resistors
    [Solenoids.kicad_sch]
2025-10-08 Added Power Status LEDs
    [Power.kicad_sch, Solenoids.kicad_sch]
2025-10-09 Not Entirely Sure
    [ADCs.kicad_sch, Accelerometer.kicad_sch, Alpha_Breakout.kicad_pcb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]
2025-10-09 Connected solenoids, some error fixes
    [Alpha_Breakout.kicad_sch, stm32f1.kicad_sch, thermoAms.kicad_sch]
2025-10-09 read description
    [ADS1231.kicad_sch, ADS1231ID.step, Alpha_Breakout.kicad_pcb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]
2025-10-09 arranged board
    [Alpha_Breakout.kicad_pcb, Alpha_Breakout.kicad_sch, BM02B-GHS-TBT_LF__SN_.step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]
2025-10-09 estop added
    [Alpha_Breakout.kicad_pcb, Solenoids.kicad_sch]
2025-10-10 Added Load Cell IC and Circuitry, fixed wacked out symbol
    [ADS1231.kicad_sch, Alpha_Breakout.csv]
2025-10-12 Load Cell
    [Power.kicad_sch]
2025-10-12 added leds🔴🟡🔵
    [ADCs.kicad_sch, ADS1231.kicad_sch, Accelerometer.kicad_sch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]
2025-10-13 lots🅿️
    [ADCs.kicad_sch, ADS1231.kicad_sch, Alpha_Breakout.kicad_pcb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]
2025-10-13 bunchostuff💐
    [Alpha_Breakout.kicad_pcb, Hardware_Safe.kicad_sch, Pyro.kicad_sch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]
2025-10-13 Added Golden Dome yay
    [Alpha_Breakout.kicad_pcb]
2025-10-13 done ✅
    [ADS1231.kicad_sch, Accelerometer.kicad_sch, Alpha_Breakout.kicad_pcb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]
2025-10-13 settings ⚙️
    [Alpha_Breakout.kicad_pcb]
2025-10-14 Moved Mary to avoid MCU
    [Alpha_Breakout.kicad_pcb]
2025-10-15 ROuted 5V Power
    [Alpha_Breakout.kicad_pcb]
2025-10-15 routed initial🛣️
    [Alpha_Breakout.kicad_pcb]
2025-10-15 3.3 partially routed, to avoid signal
    [Alpha_Breakout.kicad_pcb, Power.kicad_sch]
2025-10-16 Routed some stuff
    [Alpha_Breakout.kicad_pcb]
2025-10-16 More Routing
    [Alpha_Breakout.kicad_pcb]
2025-10-16 First Draft of BOM
    Didn't select some compoentns like diodes that I don't fully understand. Also, some components have multiple variants so we must be careful.
    [ADCs.kicad_sch, ADS1231.kicad_sch, Accelerometer.kicad_sch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]
2025-10-16 Finished draft of MOST signal routing, except for Pyro/noids channels
    [Alpha_Breakout.kicad_pcb]
2025-10-16 parts⚙️
    [ADCs.kicad_sch, ADS1231.kicad_sch, Accelerometer.kicad_sch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]
2025-10-16 3.3v Routed
    [Alpha_Breakout.kicad_pcb]
2025-10-17 Routed Ground, except for one pad
    [Alpha_Breakout.kicad_pcb]
2025-10-27 clearance🎣
    [Alpha_Breakout.kicad_pcb]
2025-10-27 fixed warnings⚠️
    [Alpha_Breakout.kicad_pcb, stm32f1.kicad_sch]
2025-10-28 touchups 💅
    [ADCs.kicad_sch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]
2025-10-28 fixed usb 🔌
    [Alpha_Breakout.kicad_pcb, prog.kicad_sch]
2025-10-28 added version 🚅
    [Alpha_Breakout.kicad_pcb]
2025-10-28 changed noid fets🎚️
    [Alpha_Breakout.kicad_pcb, SI2302.step, Solenoids.kicad_sch]
2025-10-29 v1.0 DONE6️⃣7️⃣🚀⚡️🔋
    [Alpha_Breakout.kicad_pcb, Power.kicad_sch]
2025-11-06 productio ⚙️
    [Alpha_Breakout-B_Cu.gbr, Alpha_Breakout-B_Mask.gbr, Alpha_Breakout-B_Paste.gbr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]
